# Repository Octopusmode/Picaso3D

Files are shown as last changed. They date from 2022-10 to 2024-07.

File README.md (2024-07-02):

# Typing SVG (https://git.io/typing-svg)

В этом репозитории находятся полезные ресурсы для принтеров [Picaso3D](https://picaso-3d.ru/ru/techsupport/).

Репозиторий поддерживается участниками телеграм-группы [Picaso3dUnofficial](https://t.me/Picaso3dUnofficial).

Официальный сайт [Центра поддержки Picaso3D](http://helpcenter.picaso-3d.ru/).

## Содержимое репозитория:
#### :large_blue_circle: [Hardware (Фотографии плат, покупные радиоэлементы)](./Hardware)
---
  * [DES](./Hardware/DES_Hardware)
  * [DPXL](./Hardware/DPXL_Hardware)
  * [DXL](./Hardware/DXL_Hardware)
  * [DPX](./Hardware/DPX_Hardware)
    * [DPX_DPXL_Мотор_переключения_сопел](./Hardware/DPX_Hardware/DPX_DPXL_Мотор_переключения_сопел)
    * [DPX_Electronic_components](./Hardware/DPX_Hardware/DPX_Electronic_components)
    * [DPX_Motherboard](./Hardware/DPX_Hardware/DPX_Motherboard)
    * [DPX_Ремень](./Hardware/DPX_Hardware/DPX_Ремень)
    * [DPX_Энкодер](./Hardware/DPX_Hardware/DPX_Энкодер)
  * [DPX_S2](./Hardware/DPX_S2_Hardware)
  * [DXL_S2](./Hardware/DXL_S2_Hardware)
  * [DX](./Hardware/DX_Hardware)
  * [DX_S2](./Hardware/DX_S2_Hardware)
  * [PRO250](./Hardware/PRO250_Hardware)
 * [Покупные_радиоэлементы_разное](./Hardware/Покупные_радиоэлементы_разное)
    * [Муфта](./Hardware/Покупные_радиоэлементы_разное/Муфта)
    * [Ссылки](./Hardware/Покупные_радиоэлементы_разное/Ссылки)
    * [Фотографии](./Hardware/Покупные_радиоэлементы_разное/Фотографии)

#### :large_blue_circle: [Software (Программное обеспечение, прошивки)](./Software)
---
  * [PRO250_EEPROM](./Software/PRO250_EEPROM_(uc))
  * [PRO250_Прошивки](./Software/PRO250_Прошивки)
  * [DES_Klipper_cfg](./Software/DES_Klipper_cfg)
  * [DES_Marlin_cfg](./Software/DES_Marlin_cfg)
  * [DES_Прошивка](./Software/DES_Прошивка)
  * [XPRO_Прошивки](./Software/XPRO_Прошивки)
  * [PolygonX](./Software/PolygonX)
  * [PRO250_Klipper_(external_link)](https://github.com/Octopusmode/pro250)
  * [Утилита_для_удаленной_печати_(external_link)](https://github.com/olegh/pxctl) 

#### :large_blue_circle: STL-файлы для ремонта принтера, тюнинга, файлы для калибровки
---
  * [STL_Детали_принтеров](./STL_Детали_принтеров)
<details>
<summary> Список файлов в папке "STL_Детали_принтеров" </summary>
 
   * [PRO250](./STL_Детали_принтеров/PRO250)
     * [PRO250_HolderUpgrade](./STL_Детали_принтеров/PRO250/PRO250_HolderUpgrade)
     * [PRO250_Filament_Feeder](./STL_Детали_принтеров/PRO250/PRO250_Filament_Feeder.stl)
     * [PRO250_Y_endstop](./STL_Детали_принтеров/PRO250/PRO250_Y_endstop.stl)
     * [PRO250_Y_Shaft_holder](./STL_Детали_принтеров/PRO250/PRO250_Y_Shaft_holder.stl)
     * [PRO250_Кронштейн](./STL_Детали_принтеров/PRO250/PRO250_Кронштейн.stl)
     * [PRO250_Крутилка_стола](./STL_Детали_принтеров/PRO250/PRO250_Крутилка_стола.stl)
     * [PRO250_Сборка_головы](./STL_Детали_принтеров/PRO250/PRO250_Сборка_головы.stp)
     * [PRO250_Центральная_шестерня.pdf](./STL_Детали_принтеров/PRO250/PRO250_Центральная_шестерня.pdf)
     * [DPS_004.10.08_Филамент](./STL_Детали_принтеров/PRO250/DPS_004.10.08_Филамент.stl)
     * [Держатель_очистителя_PRO250_под_очиститель_X_PRO_repaired_fixed](./STL_Детали_принтеров/PRO250/Держатель_очистителя_PRO250_под_очиститель_X_PRO_repaired_fixed.stl)
     * [Контейнер_под_держатель_чистика](./STL_Детали_принтеров/PRO250/Контейнер_под_держатель_чистика.stl)
     * [Упор_концевика](./STL_Детали_принтеров/PRO250/Упор_концевика.stl)
     * [Шайба_двигателя_переключения_сопел](./STL_Детали_принтеров/PRO250/Шайба_двигателя_переключения_сопел.stl)
  * [Designer](./STL_Детали_принтеров/Designer)
  * [DES_Кронштейн](./STL_Детали_принтеров/DES_Кронштейн.stl)
  * [DES_Проставка_экструдер](./STL_Детали_принтеров/DES_Проставка_экструдер.stl)
  * [DESС_00.00.03_Петля_верхняя_скрытая](./STL_Детали_принтеров/DESС_00.00.03_Петля_верхняя_скрытая.stl)
  * [DESС_00.00.04_Петля_нижняя_скрытая](./STL_Детали_принтеров/DESС_00.00.04_Петля_нижняя_скрытая.stl)
  * [DESС_00.00.06_Петля_средняя_скрытая](./STL_Детали_принтеров/DESС_00.00.06_Петля_средняя_скрытая.stl)
  * [DPS_004.10.08_Филамент](./STL_Детали_принтеров/DPS_004.10.08_Филамент.stl)
  * [DPS_004.10.09_Держатель_трубок](./STL_Детали_принтеров/DPS_004.10.09_Держатель_трубок.stl)
  * [DPS_01.00.14_Левый_зажим_эксцентрик](./STL_Детали_принтеров/DPS_01.00.14_Левый_зажим_эксцентрик.stl)
  * [DPS_01.00.14_Правый_зажим_эксцентрик.](./STL_Детали_принтеров/DPS_01.00.14_Правый_зажим_эксцентрик.stl)
  * [DPS_02.00.02_01_Стойка_для_валов_XY](./STL_Детали_принтеров/DPS_02.00.02_01_Стойка_для_валов_XY.stl)
  * [DPS_02.00.08.01_Держатель_трубки](./STL_Детали_принтеров/DPS_02.00.08.01_Держатель_трубки.stl)
  * [DPS_02.00.08_01_Держатель_трубки_](./STL_Детали_принтеров/DPS_02.00.08_01_Держатель_трубки_.stl)
  * [DPS_02.00.09_Держатель_чистика](./STL_Детали_принтеров/DPS_02.00.09_Держатель_чистика.stl)
  * [DEX_Фиксатор_трубки_подачи_пластика](./STL_Детали_принтеров/DEX_Фиксатор_трубки_подачи_пластика.stl)  
  * [DPX_00.00.05_Держатель_катушки](./STL_Детали_принтеров/DPX_00.00.05_Держатель_катушки.stl)
  * [DPX_02.00.02_Держатель_роликов_левый](./STL_Детали_принтеров/DPX_02.00.02_Держатель_роликов_левый.stl)
  * [DPX_02.00.03_Держатель_роликов_правый](./STL_Детали_принтеров/DPX_02.00.03_Держатель_роликов_правый.stl)
  * [DPX_02.00.04_Втулка_правого_держателя](./STL_Детали_принтеров/DPX_02.00.04_Втулка_правого_держателя.stl)
  * [DPX_02.00.05_Втулка_дистанционная_new](./STL_Детали_принтеров/DPX_02.00.05_Втулка_дистанционная_new.stl)
  * [DPX_02.00.16_Держатель_чистика_V1](./STL_Детали_принтеров/DPX_02.00.16_Держатель_чистика_V1.stl)
  * [DPX_04.00.03_Крутилка](./STL_Детали_принтеров/DPX_04.00.03_Крутилка.stl)
  * [DPX_Держатель_пружины](./STL_Детали_принтеров/DPX_Держатель_пружины.stl)
  * [DPX_Держатель_трубки_v1](./STL_Детали_принтеров/DPX_Держатель_трубки_v1.stl)
  * [DPX_Фиксатор_трубок_подачи_пластика](./STL_Детали_принтеров/DPX_Фиксатор_трубок_подачи_пластика.stl)
  * [DPX_Чистик](./STL_Детали_принтеров/DPX_Чистик.stl)
  * [DPX_Блоки_энкодеров_S1_S2](./STL_Детали_принтеров/DPX_Блоки_энкодеров_S1_S2)
  * [DXL_DPXL_Боковой_фиксатор_трубки_подачи_пластика](./STL_Детали_принтеров/DXL_DPXL_Боковой_фиксатор_трубки_подачи_пластика.stl)
  * [DXL_Воздуховод](./STL_Детали_принтеров/DXL_Воздуховод.stl)
  * [DXL_Воздуховод_short](./STL_Детали_принтеров/DXL_Воздуховод_short.stl)
  * [DXL_Заглушка](./STL_Детали_принтеров/DXL_Заглушка.stl)
  * [DXL_Фиксатор_винта_М4](./STL_Детали_принтеров/DXL_Фиксатор_винта_М4.stl)
  * [DXL_Блок_энкодера](./STL_Детали_принтеров/DXL_Блок_энкодера)
  * [DPXL_Фиксатор_прижимного_винта_М4.](./STL_Детали_принтеров/DPXL_Фиксатор_прижимного_винта_М4.stl)
  * [DX_02.00.09_Держатель_чистика.](./STL_Детали_принтеров/DX_02.00.09_Держатель_чистика.stl)
  * [DX_radfan_v1.0](./STL_Детали_принтеров/DX_radfan_v1.0.stl)
  * [DX_Держатель_прижимной_пружины](./STL_Детали_принтеров/DX_Держатель_прижимной_пружины.stl)
  * [DX_Держатель_пружины](./STL_Детали_принтеров/DX_Держатель_пружины.stl)
  * [DX_Блок_энкодера_Корпус](./STL_Детали_принтеров/DX_Блок_энкодера_Корпус)
  * [DX_Проставка_радиатора](./STL_Детали_принтеров/DX_Проставка_радиатора)
  * [DX_DPX_Рычаг_диска_энкодера](./STL_Детали_принтеров/DX_DPX_Рычаг_диска_энкодера.stl)
  * [SDX_Направляющая_пластика](./STL_Детали_принтеров/SDX_Направляющая_пластика.stl)
  * [SDPX_Корпус_блока_энкодеров](./STL_Детали_принтеров/SDPX_Корпус_блока_энкодеров.stl)
  * [Воздуховод](./STL_Детали_принтеров/Воздуховод.stl)
  * [Деталь_филамента](./STL_Детали_принтеров/Деталь_филамента.stl)
  * [Кронштейн_для_кабель_канала](./STL_Детали_принтеров/Кронштейн_для_кабель_канала.stl)
  * [Петля_в_сборе](./STL_Детали_принтеров/Петля_в_сборе.stl)
  * [Сухари](./STL_Детали_принтеров/Сухари)
  * [Шайба_двигателя_переключения_сопел](./STL_Детали_принтеров/Шайба_двигателя_переключения_сопел.stl)
  * [Шайба_двигателя_переключения_сопел](./STL_Детали_принтеров/Шайба_двигателя_переключения_сопел) 
</details>

  * [STL_Калибровочные_шаблоны](./STL_Калибровочные_шаблоны)

<details>
<summary> Список файлов в папке "STL_Калибровочные_шаблоны" </summary>
 
  * [PRO250_Сведение_сопел](./STL_Калибровочные_шаблоны/PRO250_Сведение_сопел)
  * [PRO250_Тест_ремней](./STL_Калибровочные_шаблоны/PRO250_Тест_ремней)
  * [Калибровочный_шаблон_очистителя](./STL_Калибровочные_шаблоны/Калибровочный_шаблон_очистителя.stl)
  * [Калибровочный_шаблон_очистителя_0XYn](./STL_Калибровочные_шаблоны/Калибровочный_шаблон_очистителя_0XYn.stl)
  * [Калибровочный_шаблон_очистителя_XY0.plgx](./STL_Калибровочные_шаблоны/Калибровочный_шаблон_очистителя_XY0.plgx)
  * [Настройка_прижима](./STL_Калибровочные_шаблоны/Настройка_прижима.stl)
  * [Настройка_прижима_200x200](./STL_Калибровочные_шаблоны/Настройка_прижима_200x200.stl)
  * [Настройка_прижима_куб_2х2х2](./STL_Калибровочные_шаблоны/Настройка_прижима_куб_2х2х2.stl)
  * [Настройка_прижима_ХPRO_0.25.plgx](./STL_Калибровочные_шаблоны/Настройка_прижима_ХPRO_0.25.plgx)
  * [Сведение_сопел_0.3.plgx](./STL_Калибровочные_шаблоны/Сведение_сопел_0.3.plgx)
  * [Сведение_сопел_ABS.plg](./STL_Калибровочные_шаблоны/Сведение_сопел_ABS.plg)
  * [Сведение_сопел_PLA.plg](./STL_Калибровочные_шаблоны/Сведение_сопел_PLA.plg)
  * [Сведение_сопел_грубо.plgx](./STL_Калибровочные_шаблоны/Сведение_сопел_грубо.plgx)
  * [Сведение_сопел_грубо_полный.plgx](./STL_Калибровочные_шаблоны/Сведение_сопел_грубо_полный.plgx)
  * [Сведение_сопел_кольца_0_25_0_5.plgx](./STL_Калибровочные_шаблоны/Сведение_сопел_кольца_0_25_0_5.plgx)
</details>

  * [STL_Тюнинг](./STL_Тюнинг)
<details>
<summary> Список файлов в папке "STL_Тюнинг" </summary>
 
  * [DPXL_Фиксатор_трубок_подачи_пластика](./STL_Тюнинг/DPXL_Фиксатор_трубок_подачи_пластика)
  * [DPX_Фиксатор_трубок_подачи_пластика_mod3](./STL_Тюнинг/DPX_Фиксатор_трубок_подачи_пластика_mod3)
  * [DPX_S2_Фиксатор_трубок_подачи_пластика](./STL_Тюнинг/DPX_S2_Фиксатор_трубок_подачи_пластика)
  * [DX_S2_Фиксатор_трубок_подачи_пластика](./STL_Тюнинг/DX_S2_Фиксатор_трубок_подачи_пластика)
  * [DX_Вентиляторы_обдува_детали](./STL_Тюнинг/DX_Вентиляторы_обдува_детали)
  * [DX_Фиксатор_трубок_подачи_для_Формакс](./STL_Тюнинг/DX_Фиксатор_трубок_подачи_для_Формакс)
  * [DXL_DPXL_Крепление_стекла](./STL_Тюнинг/DXL_DPXL_Крепление_стекла)
  * [DXL_DPXL_Центровщик_флешки_для_принтера](./STL_Тюнинг/DXL_DPXL_Центровщик_флешки_для_принтера.stl)
  * [DXL_Воздухоотвод_для_принтера](./STL_Тюнинг/DXL_Воздухоотвод_для_принтера.stl)
  * [Контейнеры_для_мусора](./STL_Тюнинг/Контейнеры_для_мусора)
  * [Крепление_трубки_подачи](./STL_Тюнинг/Крепление_трубки_подачи)
  * [Кронштейн_для_катушки_0](./STL_Тюнинг/Кронштейн_для_катушки_0)
  * [Кронштейн_для_катушки_1](./STL_Тюнинг/Кронштейн_для_катушки_1)
  * [Кронштейн_для_катушки_3](./STL_Тюнинг/Кронштейн_для_катушки_3)
  * [Кронштейн_для_катушки_4](./STL_Тюнинг/Кронштейн_для_катушки_4)
  * [Кронштейн_для_катушки_5](./STL_Тюнинг/Кронштейн_для_катушки_5)
  * [Фильтры_пыли](./STL_Тюнинг/Фильтры_пыли)
  * [Filament_tube_feeder](./STL_Тюнинг/Filament_tube_feeder.stl)
  * [Держатель_для_ключа_сопла](./STL_Тюнинг/Держатель_для_ключа_сопла.stl)
</details>

#### :large_blue_circle: Инструкции
---
  * [Подшипники_S1](./Подшипники_S1)
  * [Инструкции](./Инструкции)

<details>
<summary> Список инструкций </summary>
 
  * [Builder_Picaso_инструкция.pdf](./Инструкции/Builder_Picaso_инструкция.pdf)
  * [DES_PRO250_Замена_ремней](./Инструкции/DES_PRO250_Замена_ремней)
  * [DES_PRO250_Ошибка_DEF_DEF.pdf](./Инструкции/DES_PRO250_Ошибка_DEF_DEF.pdf)
  * [DES_PRO250_Почему_не_подается_пластик.pdf](./Инструкции/DES_PRO250_Почему_не_подается_пластик.pdf)
  * [DES_PRO250_Сборка_нагревателя.pdf](./Инструкции/DES_PRO250_Сборка_нагревателя.pdf)
  * [DES_Замена_роликов_швеллер.pdf](./Инструкции/DES_Замена_роликов_швеллер.pdf)
  * [DES_Прочистка_трубки_нагревательного_элемента.pdf](./Инструкции/DES_Прочистка_трубки_нагревательного_элемента.pdf)
  * [PRO250_Калибровка_сопел_совмещение.pdf](./Инструкции/PRO250_Калибровка_сопел_совмещение.pdf)
  * [PRO250_Настройка_датчика_стола.pdf](./Инструкции/PRO250_Настройка_датчика_стола.pdf)
  * [PRO250_Проверка_напряжений_на_моторах.pdf](./Инструкции/PRO250_Проверка_напряжений_на_моторах.pdf)
  * [PRO250_Прочистка_нагревателя.pdf](./Инструкции/PRO250_Прочистка_нагревателя.pdf)
  * [PRO250_Разборка_головы.pdf](./Инструкции/PRO250_Разборка_головы.pdf)
  * [PRO250_Утилита_Service_exe_Калибровка_сопел_совмещение](./Инструкции/PRO250_Утилита_Service_exe_Калибровка_сопел_совмещение)
  * [X_Диагностика_блока_энкодеров.pdf](./Инструкции/X_Диагностика_блока_энкодеров.pdf)
  * [X_XPRO_Замена_заднего_крепления_стекла_.pdf](./Инструкции/X_XPRO_Замена_заднего_крепления_стекла_.pdf)
  * [X_XPRO_Настройка_стола.docx.pdf](./Инструкции/X_XPRO_Настройка_стола.docx.pdf)
  * [XPRO_Неполный_разбор_печатающей_головы.pdf](./Инструкции/XPRO_Неполный_разбор_печатающей_головы.pdf)
  * [XPRO_Проверка_замена_роликов_и_ремней.pdf](./Инструкции/XPRO_Проверка_замена_роликов_и_ремней.pdf)
  * [XPRO_Прочистка_нагревателя.pdf](./Инструкции/XPRO_Прочистка_нагревателя.pdf)
  * [XPRO_Список_ошибок.pdf](./Инструкции/XPRO_Список_ошибок.pdf)
  * [XL_XLPRO_Настройка_ШВП.pdf](./Инструкции/XL_XLPRO_Настройка_ШВП.pdf)
  * [Инструкция_по_упаковке_принтеров.pdf](./Инструкции/Инструкция_по_упаковке_принтеров.pdf)
  * [Инструкция_ШС_Шкаф_Сушильный.pdf](./Инструкции/Инструкция_ШС_Шкаф_Сушильный.pdf)

 </details>

#### :large_blue_circle: Настройки слайсеров, профили пластиков
---
  * [Cura](./_Cura)
  * [S3D_для_Picaso_Статья_о_настройке](./_S3D_для_Picaso_Статья_о_настройке)
  * [Профили_Polygon_XPRO](./Профили_пластиков_S3D_Polygon/Профили_Polygon_XPRO)

<details>
<summary>Список профилей для Polygon для XPRO</summary>

1. ABSM_PETG
1. BESTF_ABS
1. BESTF_PLA_BLACK
1. ESUN_ABS
1. ESUN_PLA_200
1. ESUN_PLA
1. FILM_CERAMO
1. FILM_SBS
1. FLEX_HARD PprintProduct
1. NYLON_MOD_PprintProduct
1. NYLON STRONG_PP
1. PICASO_ABS
1. PICASO_HIPS
1. PICASO_PLA
1. PICASO PVA(ESUN)
1. PICASO_PVA(REC)
1. PLA_PrintProduct
1. REC_ABS
1. REC_FLEX
1. REC_HIPS
1. REC_PLA
1. TAULMAN_910
1. U3PRINT_PC
1. VOLPRINT_PLA

</details>

  * [Профили_Simplify3D](./Профили_пластиков_S3D_Polygon/Профили_Simplify3D)

<details>
<summary>Список профилей для Simplify3D для DPX, DX</summary>

1. all_profiles_DX_DXP.factory
1. Picaso_DPX_ABS-PA+HIPS_script.fff
1. Picaso_DPX_FlexHARD+PLA(F).fff
1. Picaso_DPX_F_WAX3D.fff
1. Picaso_DPX_GF4+HIPS_script.fff
1. Picaso_DPX_PETG(BF)+PLA(F).fff
1. Picaso_DPX_PETG+PLA(F)_script.fff
1. Picaso_DPX_PLA+PVA(eSUN).fff
1. Picaso_DPX_PLA+PVA(REC).fff
1. Picaso_DPX_TPU(A75)+PLA(F).fff
1. Picaso_DPX_TPU(A80)+PLA(F).fff
1. Picaso_DPX_TPU(A93)+PLA(F).fff
1. Picaso_DX_ABS_LITHOPANE.fff
1. Picaso_DX_BF_PLA.fff
1. Picaso_DX_CLOTHO-ABS-GF13.fff
1. Picaso_DX_eSUN_ePA-CF.fff
1. Picaso_DX_FD_TPU-A75.fff
1. Picaso_DX_F_ABS-PA-GF8.fff
1. Picaso_DX_F_ABS-PA.fff
1. Picaso_DX_F_ABS.fff
1. Picaso_DX_F_CERAMO.fff
1. Picaso_DX_F_GF4.fff
1. Picaso_DX_F_PA66-GF30.fff
1. Picaso_DX_F_PBT-GF30.fff
1. Picaso_DX_F_PETg.fff
1. Picaso_DX_F_PLA.fff
1. Picaso_DX_F_PP-GF30.fff
1. Picaso_DX_F_PP.fff
1. Picaso_DX_F_PRO-FLEX.fff
1. Picaso_DX_F_SBS.fff
1. Picaso_DX_F_TERMAX-GF40.fff
1. Picaso_DX_F_TITAN_ABS-GF12.fff
1. Picaso_DX_F_TPU-A80.fff
1. Picaso_DX_F_TPU-A93.fff
1. Picaso_DX_F_TPU-CF5.fff
1. Picaso_DX_F_TPU-GF10.fff
1. Picaso_DX_F_TPU-GF30.fff
1. Picaso_DX_HTP_NYLON.fff
1. Picaso_DX_IGUS_J260.fff
1. Picaso_DX_PrPr_FlexHARD.fff
1. Picaso_DX_REC_FORMAX.fff
1. Picaso_DX_REC_RUBBER.fff
1. Picaso_DX_REC_TPU-D70.fff

</details>

  * [Профили_Simplify_PRO250](./Профили_пластиков_S3D_Polygon/Профили_Simplify_PRO250)

<details>
<summary>Список профилей для Simplify3D для PRO250</summary>

1. Picaso ABS 0.8.fff
1. PICASO ABS 2 heads support dens.fff
1. Picaso Designer PRO250.fff
1. PICASO DUAL COLOR.fff
1. PRO250 ABS 0.3 color_A.fff
1. PRO250 ABS 0.3 color_B.fff
1. PRO250 ABS 1 head 0.3.fff
1. PRO250 ABS_HIPS 2hds 85dens.fff
1. PRO250 ABS_PC 0.3 1extruder.fff
1. PRO250 SBS 0.8 transparent-Bottle Small.fff
1. PRO250 SBS 0.8 transparent-Bottle.fff

</details>

#### :large_blue_circle: Ремонт, тюнинг
---
  * [Сопливчик_форма_для_литья](./Сопливчик_форма_для_литья)
  * [Стёкла](./Стёкла)
    * [250PRO_стекло_0.jpg](./Стёкла/img/250PRO_стекло_0.jpg)
    * [250PRO_стекло_1.jpg](./Стёкла/img/250PRO_стекло_1.jpg)
    * [XPRO_Стекло_0.jpg](./Стёкла/img/XPRO_Стекло_0.jpg)
    * [XPRO_Стекло_1.jpg](./Стёкла/img/XPRO_Стекло_1.jpg)
    * [XL_glass.jpg](./Стёкла/img/XL_glass.jpg)
  * [Листы_PEI](./Листы_PEI)
  * [Тензодатчик](./Тензодатчик)

#### :large_blue_circle: Справочное
---
  * [Сушка_пластика](./Сушка_пластика)
  * [Термопаста_смазки](./Термопаста_смазки) 
  * [Размеры_масса_катушек_филамента.xlsx](./Размеры_масса_катушек_филамента.xlsx)

#### :large_blue_circle: Разное
---
  * [Картонная_катушка_HTP](./Картонная_катушка_HTP)
  * [Несортированное](./Несортированное)

#### :large_blue_circle: Используемые сокращения
---
> **PRO250** Designer PRO250
> 
> **DES** Designer
> 
> **DESC** Designer Classic
> 
> **DX** Designer X
> 
> **DXPRO DPX** Designer X PRO
>
> **DXL** Designer XL
>
> **DXLPRO DPXL** Designer XL PRO
>
> **SDPX** Designer X PRO S2
>
> **SDX** Designer X S2

> Информация о принтерах X, XPRO, XL, XLPRO без пометки «S2» относится к принтерам серии «S1».

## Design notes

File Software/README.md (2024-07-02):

# Software/программное обеспечение принтеров Picaso

В данном разделе хранятся:

+ конфиги прошивок Marlin, Klipper для родных плат принтера Picaso Designer;

+ файлы прошивок принтеров, в том числе PRO250;

+ файлы старых версий PolygonX;

+ прочее, связанное с программным обеспечением принтеров.

Внешние ссылки:

 * PRO250_Klipper: https://github.com/Octopusmode/pro250

 * Утилита_для_удаленной_печати: https://github.com/olegh/pxctl

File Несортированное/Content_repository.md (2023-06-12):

# Содержимое репозитория:

## [Firmware (Фотографии плат, покупные радиоэлементы)](./Firmware)

  * [DES](./Firmware/DES_Firmware)
  * [DPXL](.Firmware/DPXL_Firmware)
    * [XLPRO_XPRO_Мотор_переключения_сопел](./Firmware/DPXL_Firmware/XLPRO_XPRO_Мотор_переключения_сопел.lnk)
  * [DPX](./Firmware/DPX_Firmware_(under_construction))
    * [DPX_DPXL_Мотор_переключения_сопел](./Firmware/DPX_Firmware_(under_construction)/DPX_DPXL_Мотор_переключения_сопел)
    * [DPX_Electronic_components](./Firmware/DPX_Firmware_(under_construction)/DPX_Electronic_components)
    * [DPX_Motherboard](./Firmware/DPX_Firmware_(under_construction)/DPX_Motherboard)
    * [DPX_Ремень](./Firmware/DPX_Firmware_(under_construction)/DPX_Ремень)
    * [DPX_Энкодер](./Firmware/DPX_Firmware_(under_construction)/DPX_Энкодер)
  * [DPX_S2](./Firmware/DPX_S2_Firmware)
  * [DXL_S2](./Firmware/DXL_S2_Firmware)
  * [DX](./Firmware/DX_Firmware_(under_construction))
  * [DX_S2](./Firmware/DX_S2_Firmware)
  * [PRO250](./Firmware/PRO250_Firmware)
  * [Покупные_радиоэлементы_разное](./Firmware/Покупные_радиоэлементы_разное)
    * [Муфта](./Firmware/Покупные_радиоэлементы_разное/Муфта)
    * [Ссылки](./Firmware/Покупные_радиоэлементы_разное/Ссылки)
    * [Фотографии](./Firmware/Покупные_радиоэлементы_разное/Фотографии)

## [Software (Программное обеспечение, прошивки)](./Software)

  * [PRO250_EEPROM](./Software/PRO250_EEPROM (uc))
  * [PRO250_Прошивки](./Software/PRO250_Прошивки)
  * [DES_Klipper_cfg](./Software/DES_Klipper_cfg)
  * [DES_Marlin_cfg](./Software/DES_Marlin_cfg)
  * [XPRO_Прошивки](./Software/XPRO_Прошивки)
  * [PolygonX](./Software/PolygonX)

## STL-файлы для ремонта принтера, тюнинга, файлы для калибровки

### [STL_Детали_принтеров](./STL_Детали_принтеров)

   * [PRO250](./STL_Детали_принтеров/PRO250)
     * [PRO250_HolderUpgrade](./STL_Детали_принтеров/PRO250/PRO250_HolderUpgrade)
     * [PRO250_Filament_Feeder](./STL_Детали_принтеров/PRO250/PRO250_Filament_Feeder.stl)
     * [PRO250_Y_endstop](./STL_Детали_принтеров/PRO250/PRO250_Y_endstop.stl)
     * [PRO250_Y_Shaft_holder](./STL_Детали_принтеров/PRO250/PRO250_Y_Shaft_holder.stl)
     * [PRO250_Кронштейн](./STL_Детали_принтеров/PRO250/PRO250_Кронштейн.stl)
     * [PRO250_Крутилка_стола](./STL_Детали_принтеров/PRO250/PRO250_Крутилка_стола.stl)
     * [PRO250_Сборка_головы](./STL_Детали_принтеров/PRO250/PRO250_Сборка_головы.stp)
     * [PRO250_Центральная_шестерня.pdf](./STL_Детали_принтеров/PRO250/PRO250_Центральная_шестерня.pdf)
     * [DPS_004.10.08_Филамент](./STL_Детали_принтеров/PRO250/DPS_004.10.08_Филамент.stl)
     * [Держатель_очистителя_PRO250_под_очиститель_X_PRO_repaired_fixed](./STL_Детали_принтеров/PRO250/Держатель_очистителя_PRO250_под_очиститель_X_PRO_repaired_fixed.stl)
     * [Контейнер_под_держатель_чистика](./STL_Детали_принтеров/PRO250/Контейнер_под_держатель_чистика.stl)
     * [Упор_концевика](./STL_Детали_принтеров/PRO250/Упор_концевика.stl)
     * [Шайба_двигателя_переключения_сопел](./STL_Детали_принтеров/PRO250/Шайба_двигателя_переключения_сопел.stl)
  
  * [DES_Кронштейн](./STL_Детали_принтеров/DES_Кронштейн.stl)
  * [DES_Проставка_экструдер](./STL_Детали_принтеров/DES_Проставка_экструдер.stl)

  * [DESС_00.00.03_Петля_верхняя_скрытая](./STL_Детали_принтеров/DESС_00.00.03_Петля_верхняя_скрытая.stl)
  * [DESС_00.00.04_Петля_нижняя_скрытая](./STL_Детали_принтеров/DESС_00.00.04_Петля_нижняя_скрытая.stl)
  * [DESС_00.00.06_Петля_средняя_скрытая](./STL_Детали_принтеров/DESС_00.00.06_Петля_средняя_скрытая.stl)

  * [DPS_004.10.08_Филамент](./STL_Детали_принтеров/DPS_004.10.08_Филамент.stl)
  * [DPS_004.10.09_Держатель_трубок](./STL_Детали_принтеров/DPS_004.10.09_Держатель_трубок.stl)
  * [DPS_01.00.14_Левый_зажим_эксцентрик](./STL_Детали_принтеров/DPS_01.00.14_Левый_зажим_эксцентрик.stl)
  * [DPS_01.00.14_Правый_зажим_эксцентрик.](./STL_Детали_принтеров/DPS_01.00.14_Правый_зажим_эксцентрик.stl)
  * [DPS_02.00.02_01_Стойка_для_валов_XY](./STL_Детали_принтеров/DPS_02.00.02_01_Стойка_для_валов_XY.stl)
  * [DPS_02.00.08.01_Держатель_трубки](./STL_Детали_принтеров/DPS_02.00.08.01_Держатель_трубки.stl)
  * [DPS_02.00.08_01_Держатель_трубки_](./STL_Детали_принтеров/DPS_02.00.08_01_Держатель_трубки_.stl)
  * [DPS_02.00.09_Держатель_чистика](./STL_Детали_принтеров/DPS_02.00.09_Держатель_чистика.stl)

  * [DEX_Фиксатор_трубки_подачи_пластика](./STL_Детали_принтеров/DEX_Фиксатор_трубки_подачи_пластика.stl)  
  * [DPX_00.00.05_Держатель_катушки](./STL_Детали_принтеров/DPX_00.00.05_Держатель_катушки.stl)
  * [DPX_02.00.02_Держатель_роликов_левый](./STL_Детали_принтеров/DPX_02.00.02_Держатель_роликов_левый.stl)
  * [DPX_02.00.03_Держатель_роликов_правый](./STL_Детали_принтеров/DPX_02.00.03_Держатель_роликов_правый.stl)
  * [DPX_02.00.04_Втулка_правого_держателя](./STL_Детали_принтеров/DPX_02.00.04_Втулка_правого_держателя.stl)
  * [DPX_02.00.05_Втулка_дистанционная_new](./STL_Детали_принтеров/DPX_02.00.05_Втулка_дистанционная_new.stl)
  * [DPX_02.00.16_Держатель_чистика_V1](./STL_Детали_принтеров/DPX_02.00.16_Держатель_чистика_V1.stl)
  * [DPX_04.00.03_Крутилка](./STL_Детали_принтеров/DPX_04.00.03_Крутилка.stl)
  * [DPX_Держатель_пружины](./STL_Детали_принтеров/DPX_Держатель_пружины.stl)
  * [DPX_Держатель_трубки_v1](./STL_Детали_принтеров/DPX_Держатель_трубки_v1.stl)
  * [DPX_Фиксатор_трубок_подачи_пластика](./STL_Детали_принтеров/DPX_Фиксатор_трубок_подачи_пластика.stl)
  * [DPX_Чистик](./STL_Детали_принтеров/DPX_Чистик.stl)
  * [DPX_Блоки_энкодеров_S1_S2](./STL_Детали_принтеров/DPX_Блоки_энкодеров_S1_S2)
  * [DPX_Направляющая_трубки_подачи_пластика](./STL_Детали_принтеров/DPX_Направляющая_трубки_подачи_пластика)

  * [DXL_DPXL_Боковой_фиксатор_трубки_подачи_пластика](./STL_Детали_принтеров/DXL_DPXL_Боковой_фиксатор_трубки_подачи_пластика.stl)
  * [DXL_Воздуховод](./STL_Детали_принтеров/DXL_Воздуховод.stl)
  * [DXL_Воздуховод_short](./STL_Детали_принтеров/DXL_Воздуховод_short.stl)
  * [DXL_Заглушка](./STL_Детали_принтеров/DXL_Заглушка.stl)
  * [DXL_Фиксатор_винта_М4](./STL_Детали_принтеров/DXL_Фиксатор_винта_М4.stl)
  * [DXL_Блок_энкодера](./STL_Детали_принтеров/DXL_Блок_энкодера)
  * [DPXL_Фиксатор_прижимного_винта_М4.](./STL_Детали_принтеров/DPXL_Фиксатор_прижимного_винта_М4.stl)

  * [DX_02.00.09_Держатель_чистика.](./STL_Детали_принтеров/DX_02.00.09_Держатель_чистика.stl)
  * [DX_radfan_v1.0](./STL_Детали_принтеров/DX_radfan_v1.0.stl)
  * [DX_Держатель_прижимной_пружины](./STL_Детали_принтеров/DX_Держатель_прижимной_пружины.stl)
  * [DX_Держатель_пружины](./STL_Детали_принтеров/DX_Держатель_пружины.stl)
  * [DX_Блок_энкодера_Корпус](./STL_Детали_принтеров/DX_Блок_энкодера_Корпус)
  * [DX_Проставка_радиатора](./STL_Детали_принтеров/DX_Проставка_радиатора)

  * [Воздуховод](./STL_Детали_принтеров/Воздуховод.stl)
  * [Деталь_филамента](./STL_Детали_принтеров/Деталь_филамента.stl)
  * [Кронштейн_для_кабель_канала](./STL_Детали_принтеров/Кронштейн_для_кабель_канала.stl)
  * [Петля_в_сборе](./STL_Детали_принтеров/Петля_в_сборе.stl)
  * [Сухари](./STL_Детали_принтеров/Сухари)
  * [Шайба_двигателя_переключения_сопел](./STL_Детали_принтеров/Шайба_двигателя_переключения_сопел.stl)
  * [Шайба_двигателя_переключения_сопел](./STL_Детали_принтеров/Шайба_двигателя_переключения_сопел) 

### [STL_Калибровочные_шаблоны](./STL_Калибровочные_шаблоны)
 
  * [PRO250_Сведение_сопел](./STL_Калибровочные_шаблоны/PRO250_Сведение_сопел)
  * [PRO250_Тест_ремней](./STL_Калибровочные_шаблоны/PRO250_Тест_ремней)
  * [Калибровочный_шаблон_очистителя](./STL_Калибровочные_шаблоны/Калибровочный_шаблон_очистителя.stl)
  * [Калибровочный_шаблон_очистителя_0XYn](./STL_Калибровочные_шаблоны/Калибровочный_шаблон_очистителя_0XYn.stl)
  * [Калибровочный_шаблон_очистителя_XY0.plgx](./STL_Калибровочные_шаблоны/Калибровочный_шаблон_очистителя_XY0.plgx)
  * [Настройка_прижима](./STL_Калибровочные_шаблоны/Настройка_прижима.stl)
  * [Настройка_прижима_200x200](./STL_Калибровочные_шаблоны/Настройка_прижима_200x200.stl)
  * [Настройка_прижима_куб_2х2х2](./STL_Калибровочные_шаблоны/Настройка_прижима_куб_2х2х2.stl)
  * [Настройка_прижима_ХPRO_0.25.plgx](./STL_Калибровочные_шаблоны/Настройка_прижима_ХPRO_0.25.plgx)
  * [Сведение_сопел_0.3.plgx](./STL_Калибровочные_шаблоны/Сведение_сопел_0.3.plgx)
  * [Сведение_сопел_ABS.plg](./STL_Калибровочные_шаблоны/Сведение_сопел_ABS.plg)
  * [Сведение_сопел_PLA.plg](./STL_Калибровочные_шаблоны/Сведение_сопел_PLA.plg)
  * [Сведение_сопел_грубо.plgx](./STL_Калибровочные_шаблоны/Сведение_сопел_грубо.plgx)
  * [Сведение_сопел_грубо_полный.plgx](./STL_Калибровочные_шаблоны/Сведение_сопел_грубо_полный.plgx)
  * [Сведение_сопел_кольца_0_25_0_5.plgx](./STL_Калибровочные_шаблоны/Сведение_сопел_кольца_0_25_0_5.plgx)

### [STL_Тюнинг](./STL_Тюнинг)
 
  * [DPXL_Фиксатор_трубок_подачи_пластика](./STL_Тюнинг/DPXL_Фиксатор_трубок_подачи_пластика)
  * [DPX_Фиксатор_трубок_подачи_пластика_mod3](./STL_Тюнинг/DPX_Фиксатор_трубок_подачи_пластика_mod3)

  * [DX_S2_Фиксатор_трубок_подачи_пластика](./STL_Тюнинг/DX_S2_Фиксатор_трубок_подачи_пластика)

  * [DX_Вентиляторы_обдува_детали](./STL_Тюнинг/DX_Вентиляторы_обдува_детали)
  * [DX_Фиксатор_трубок_подачи_для_Формакс](./STL_Тюнинг/DX_Фиксатор_трубок_подачи_для_Формакс)

  * [DXL_DPXL_Крепление_стекла](./STL_Тюнинг/DXL_DPXL_Крепление_стекла)
  * [DXL_DPXL_Центровщик_флешки_для_принтера](./STL_Тюнинг/DXL_DPXL_Центровщик_флешки_для_принтера.stl)
  * [DXL_Воздухоотвод_для_принтера](./STL_Тюнинг/DXL_Воздухоотвод_для_принтера.stl)

  * [Контейнеры_для_мусора](./STL_Тюнинг/Контейнеры_для_мусора)
  * [Крепление_трубки_подачи](./STL_Тюнинг/Крепление_трубки_подачи)
  * [Кронштейн_для_катушки_0](./STL_Тюнинг/Кронштейн_для_катушки_0)
  * [Кронштейн_для_катушки_1](./STL_Тюнинг/Кронштейн_для_катушки_1)
  * [Кронштейн_для_катушки_3](./STL_Тюнинг/Кронштейн_для_катушки_3)
  * [Кронштейн_для_катушки_4](./STL_Тюнинг/Кронштейн_для_катушки_4)
  * [Фильтры_пыли](./STL_Тюнинг/Фильтры_пыли)

  * [Filament_tube_feeder](./STL_Тюнинг/Filament_tube_feeder.stl)
  * [Держатель_для_ключа_сопла](./STL_Тюнинг/Держатель_для_ключа_сопла.stl)

## Инструкции

### [Подшипники_S1](./Подшипники_S1)

### [Инструкции](./Инструкции)
  * [Builder_Picaso_инструкция.pdf](./Инструкции/Builder_Picaso_инструкция.pdf)

  * [DES_PRO250_Замена_ремней](./Инструкции/DES_PRO250_Замена_ремней)
  * [DES_PRO250_Ошибка_DEF_DEF.pdf](./Инструкции/DES_PRO250_Ошибка_DEF_DEF.pdf)
  * [DES_PRO250_Почему_не_подается_пластик.pdf](./Инструкции/DES_PRO250_Почему_не_подается_пластик.pdf)
  * [DES_PRO250_Сборка_нагревателя.pdf](./Инструкции/DES_PRO250_Сборка_нагревателя.pdf)
  * [DES_Замена_роликов_швеллер.pdf](./Инструкции/DES_Замена_роликов_швеллер.pdf)
  * [DES_Прочистка_трубки_нагревательного_элемента.pdf](./Инструкции/DES_Прочистка_трубки_нагревательного_элемента.pdf)
  * [PRO250_Калибровка_сопел_совмещение.pdf](./Инструкции/PRO250_Калибровка_сопел_совмещение.pdf)
  * [PRO250_Настройка_датчика_стола.pdf](./Инструкции/PRO250_Настройка_датчика_стола.pdf)
  * [PRO250_Проверка_напряжений_на_моторах.pdf](./Инструкции/PRO250_Проверка_напряжений_на_моторах.pdf)
  * [PRO250_Прочистка_нагревателя.pdf](./Инструкции/PRO250_Прочистка_нагревателя.pdf)
  * [PRO250_Разборка_головы.pdf](./Инструкции/PRO250_Разборка_головы.pdf)
  * [PRO250_Утилита_Service_exe_Калибровка_сопел_совмещение](./Инструкции/PRO250_Утилита_Service_exe_Калибровка_сопел_совмещение)

  * [X_Диагностика_блока_энкодеров.pdf](./Инструкции/X_Диагностика_блока_энкодеров.pdf)
  * [X_XPRO_Замена_заднего_крепления_стекла_.pdf](./Инструкции/X_XPRO_Замена_заднего_крепления_стекла_.pdf)
  * [X_XPRO_Настройка_стола.docx.pdf](./Инструкции/X_XPRO_Настройка_стола.docx.pdf)

  * [XPRO_Неполный_разбор_печатающей_головы.pdf](./Инструкции/XPRO_Неполный_разбор_печатающей_головы.pdf)
  * [XPRO_Проверка_замена_роликов_и_ремней.pdf](./Инструкции/XPRO_Проверка_замена_роликов_и_ремней.pdf)
  * [XPRO_Прочистка_нагревателя.pdf](./Инструкции/XPRO_Прочистка_нагревателя.pdf)
  * [XPRO_Список_ошибок.pdf](./Инструкции/XPRO_Список_ошибок.pdf)

  * [XL_XLPRO_Настройка_ШВП.pdf](./Инструкции/XL_XLPRO_Настройка_ШВП.pdf)

  * [Инструкция_по_упаковке_принтеров.pdf](./Инструкции/Инструкция_по_упаковке_принтеров.pdf)
  * [Инструкция_ШС_Шкаф_Сушильный.pdf](./Инструкции/Инструкция_ШС_Шкаф_Сушильный.pdf)

## Настройки слайсеров, профили пластиков

### [Cura](./_Cura)
  
### [S3D_для_Picaso_Статья_о_настройке](./_S3D_для_Picaso_Статья_о_настройке)

### [Профили_Polygon_XPRO](./Профили_пластиков_S3D_Polygon/Профили_Polygon_XPRO)

<details>
<summary>Список профилей для Polygon для XPRO</summary>

1. ABSM_PETG
1. BESTF_ABS
1. BESTF_PLA_BLACK
1. ESUN_ABS
1. ESUN_PLA_200
1. ESUN_PLA
1. FILM_CERAMO
1. FILM_SBS
1. FLEX_HARD PprintProduct
1. NYLON_MOD_PprintProduct
1. NYLON STRONG_PP
1. PICASO_ABS
1. PICASO_HIPS
1. PICASO_PLA
1. PICASO PVA(ESUN)
1. PICASO_PVA(REC)
1. PLA_PrintProduct
1. REC_ABS
1. REC_FLEX
1. REC_HIPS
1. REC_PLA
1. TAULMAN_910
1. U3PRINT_PC
1. VOLPRINT_PLA

</details>

### [Профили_Simplify3D](./Профили_пластиков_S3D_Polygon/Профили_Simplify3D)

<details>
<summary>Список профилей для Simplify3D для DPX, DX</summary>

1. all_profiles_DX_DXP.factory
1. Picaso_DPX_ABS-PA+HIPS_script.fff
1. Picaso_DPX_FlexHARD+PLA(F).fff
1. Picaso_DPX_F_WAX3D.fff
1. Picaso_DPX_GF4+HIPS_script.fff
1. Picaso_DPX_PETG(BF)+PLA(F).fff
1. Picaso_DPX_PETG+PLA(F)_script.fff
1. Picaso_DPX_PLA+PVA(eSUN).fff
1. Picaso_DPX_PLA+PVA(REC).fff
1. Picaso_DPX_TPU(A75)+PLA(F).fff
1. Picaso_DPX_TPU(A80)+PLA(F).fff
1. Picaso_DPX_TPU(A93)+PLA(F).fff
1. Picaso_DX_ABS_LITHOPANE.fff
1. Picaso_DX_BF_PLA.fff
1. Picaso_DX_CLOTHO-ABS-GF13.fff
1. Picaso_DX_eSUN_ePA-CF.fff
1. Picaso_DX_FD_TPU-A75.fff
1. Picaso_DX_F_ABS-PA-GF8.fff
1. Picaso_DX_F_ABS-PA.fff
1. Picaso_DX_F_ABS.fff
1. Picaso_DX_F_CERAMO.fff
1. Picaso_DX_F_GF4.fff
1. Picaso_DX_F_PA66-GF30.fff
1. Picaso_DX_F_PBT-GF30.fff
1. Picaso_DX_F_PETg.fff
1. Picaso_DX_F_PLA.fff
1. Picaso_DX_F_PP-GF30.fff
1. Picaso_DX_F_PP.fff
1. Picaso_DX_F_PRO-FLEX.fff
1. Picaso_DX_F_SBS.fff
1. Picaso_DX_F_TERMAX-GF40.fff
1. Picaso_DX_F_TITAN_ABS-GF12.fff
1. Picaso_DX_F_TPU-A80.fff
1. Picaso_DX_F_TPU-A93.fff
1. Picaso_DX_F_TPU-CF5.fff
1. Picaso_DX_F_TPU-GF10.fff
1. Picaso_DX_F_TPU-GF30.fff
1. Picaso_DX_HTP_NYLON.fff
1. Picaso_DX_IGUS_J260.fff
1. Picaso_DX_PrPr_FlexHARD.fff
1. Picaso_DX_REC_FORMAX.fff
1. Picaso_DX_REC_RUBBER.fff
1. Picaso_DX_REC_TPU-D70.fff

</details>

### [Профили_Simplify_PRO250](./Профили_пластиков_S3D_Polygon/Профили_Simplify_PRO250)

<details>
<summary>Список профилей для Simplify3D для PRO250</summary>

1. Picaso ABS 0.8.fff
1. PICASO ABS 2 heads support dens.fff
1. Picaso Designer PRO250.fff
1. PICASO DUAL COLOR.fff
1. PRO250 ABS 0.3 color_A.fff
1. PRO250 ABS 0.3 color_B.fff
1. PRO250 ABS 1 head 0.3.fff
1. PRO250 ABS_HIPS 2hds 85dens.fff
1. PRO250 ABS_PC 0.3 1extruder.fff
1. PRO250 SBS 0.8 transparent-Bottle Small.fff
1. PRO250 SBS 0.8 transparent-Bottle.fff

</details>

## Ремонт, тюнинг

### [Сопливчик_форма_для_литья](./Сопливчик_форма_для_литья)

### [Стёкла](./Стёкла)
   * [250PRO_стекло_0.jpg](./Стёкла/img/250PRO_стекло_0.jpg)
   * [250PRO_стекло_1.jpg](./Стёкла/img/250PRO_стекло_1.jpg)
   * [XPRO_Стекло_0.jpg](./Стёкла/img/XPRO_Стекло_0.jpg)
   * [XPRO_Стекло_1.jpg](./Стёкла/img/XPRO_Стекло_1.jpg)
   * [PicasoXL_glass_template_v8](./Стёкла/PicasoXL_glass_template_v8.stl)
   * [XL_glass.pdf](./Стёкла/XL_glass.pdf)

## Справочное

### [Сушка_пластика](./Сушка_пластика)
  
### [Термопаста_смазки (uc)](./Термопаста_смазки (uc))
   
### [Размеры_масса_катушек_филамента.xlsx](./Размеры_масса_катушек_филамента.xlsx)

## Разное

### [Картонная_катушка_HTP](./Картонная_катушка_HTP)

### [Листы_PEI](./Листы_PEI)

### [Несортированное](./Несортированное)

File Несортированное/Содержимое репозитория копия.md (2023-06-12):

# Содержимое репозитория:

## [Firmware (Фотографии плат, покупные радиоэлементы)](./Firmware)

  * [DES](.\Picaso3D\Firmware\DES_Firmware)
  * [DPXL](.\Picaso3D\Firmware\DPXL_Firmware)
    * [XLPRO_XPRO_Мотор_переключения_сопел](.\Picaso3D\Firmware\DPXL_Firmware\XLPRO_XPRO_Мотор_переключения_сопел.lnk)
  * [DPX](.\Picaso3D\Firmware\DPX_Firmware_(under_construction))
    * [DPX_DPXL_Мотор_переключения_сопел](.\Picaso3D\Firmware\DPX_Firmware_(under_construction)\DPX_DPXL_Мотор_переключения_сопел)
    * [DPX_Electronic_components](.\Picaso3D\Firmware\DPX_Firmware_(under_construction)\DPX_Electronic_components)
    * [DPX_Motherboard](.\Picaso3D\Firmware\DPX_Firmware_(under_construction)\DPX_Motherboard)
    * [DPX_Ремень](.\Picaso3D\Firmware\DPX_Firmware_(under_construction)\DPX_Ремень)
    * [DPX_Энкодер](.\Picaso3D\Firmware\DPX_Firmware_(under_construction)\DPX_Энкодер)
  * [DPX_S2](.\Picaso3D\Firmware\DPX_S2_Firmware)
  * [DXL_S2](.\Picaso3D\Firmware\DXL_S2_Firmware)
  * [DX](.\Picaso3D\Firmware\DX_Firmware_(under_construction))
  * [DX_S2](.\Picaso3D\Firmware\DX_S2_Firmware)
  * [PRO250](.\Picaso3D\Firmware\PRO250_Firmware)
  * [Покупные_радиоэлементы_разное](.\Picaso3D\Firmware\Покупные_радиоэлементы_разное)
    * [Муфта](.\Picaso3D\Firmware\Покупные_радиоэлементы_разное\Муфта)
    * [Ссылки](.\Picaso3D\Firmware\Покупные_радиоэлементы_разное\Ссылки)
    * [Фотографии](.\Picaso3D\Firmware\Покупные_радиоэлементы_разное\Фотографии)

## [Software (Программное обеспечение, прошивки)](.\Picaso3D\Software)

  * [PRO250_EEPROM](.\Picaso3D\Software\PRO250_EEPROM (uc))
  * [PRO250_Прошивки](.\Picaso3D\Software\PRO250_Прошивки)
  * [DES_Klipper_cfg](.\Picaso3D\Software\DES_Klipper_cfg)
  * [DES_Marlin_cfg](.\Picaso3D\Software\DES_Marlin_cfg)
  * [XPRO_Прошивки](.\Picaso3D\Software\XPRO_Прошивки)
  * [PolygonX](.\Picaso3D\Software\PolygonX)

## STL-файлы для ремонта принтера, тюнинга, файлы для калибровки

### [STL_Детали_принтеров](.\Picaso3D\STL_Детали_принтеров)

   * [PRO250](.\Picaso3D\STL_Детали_принтеров\PRO250)
     * [PRO250_HolderUpgrade](.\Picaso3D\STL_Детали_принтеров\PRO250\PRO250_HolderUpgrade)
     * [PRO250_Filament_Feeder](.\Picaso3D\STL_Детали_принтеров\PRO250\PRO250_Filament_Feeder.stl)
     * [PRO250_Y_endstop](.\Picaso3D\STL_Детали_принтеров\PRO250\PRO250_Y_endstop.stl)
     * [PRO250_Y_Shaft_holder](.\Picaso3D\STL_Детали_принтеров\PRO250\PRO250_Y_Shaft_holder.stl)
     * [PRO250_Кронштейн](.\Picaso3D\STL_Детали_принтеров\PRO250\PRO250_Кронштейн.stl)
     * [PRO250_Крутилка_стола](.\Picaso3D\STL_Детали_принтеров\PRO250\PRO250_Крутилка_стола.stl)
     * [PRO250_Сборка_головы](.\Picaso3D\STL_Детали_принтеров\PRO250\PRO250_Сборка_головы.stp)
     * [PRO250_Центральная_шестерня.pdf](.\Picaso3D\STL_Детали_принтеров\PRO250\PRO250_Центральная_шестерня.pdf)
     * [DPS_004.10.08_Филамент](.\Picaso3D\STL_Детали_принтеров\PRO250\DPS_004.10.08_Филамент.stl)
     * [Держатель_очистителя_PRO250_под_очиститель_X_PRO_repaired_fixed](.\Picaso3D\STL_Детали_принтеров\PRO250\Держатель_очистителя_PRO250_под_очиститель_X_PRO_repaired_fixed.stl)
     * [Контейнер_под_держатель_чистика](.\Picaso3D\STL_Детали_принтеров\PRO250\Контейнер_под_держатель_чистика.stl)
     * [Упор_концевика](.\Picaso3D\STL_Детали_принтеров\PRO250\Упор_концевика.stl)
     * [Шайба_двигателя_переключения_сопел](.\Picaso3D\STL_Детали_принтеров\PRO250\Шайба_двигателя_переключения_сопел.stl)
  
  * [DES_Кронштейн](.\Picaso3D\STL_Детали_принтеров\DES_Кронштейн.stl)
  * [DES_Проставка_экструдер](.\Picaso3D\STL_Детали_принтеров\DES_Проставка_экструдер.stl)

  * [DESС_00.00.03_Петля_верхняя_скрытая](.\Picaso3D\STL_Детали_принтеров\DESС_00.00.03_Петля_верхняя_скрытая.stl)
  * [DESС_00.00.04_Петля_нижняя_скрытая](.\Picaso3D\STL_Детали_принтеров\DESС_00.00.04_Петля_нижняя_скрытая.stl)
  * [DESС_00.00.06_Петля_средняя_скрытая](.\Picaso3D\STL_Детали_принтеров\DESС_00.00.06_Петля_средняя_скрытая.stl)

  * [DPS_004.10.08_Филамент](.\Picaso3D\STL_Детали_принтеров\DPS_004.10.08_Филамент.stl)
  * [DPS_004.10.09_Держатель_трубок](.\Picaso3D\STL_Детали_принтеров\DPS_004.10.09_Держатель_трубок.stl)
  * [DPS_01.00.14_Левый_зажим_эксцентрик](.\Picaso3D\STL_Детали_принтеров\DPS_01.00.14_Левый_зажим_эксцентрик.stl)
  * [DPS_01.00.14_Правый_зажим_эксцентрик.](.\Picaso3D\STL_Детали_принтеров\DPS_01.00.14_Правый_зажим_эксцентрик.stl)
  * [DPS_02.00.02_01_Стойка_для_валов_XY](.\Picaso3D\STL_Детали_принтеров\DPS_02.00.02_01_Стойка_для_валов_XY.stl)
  * [DPS_02.00.08.01_Держатель_трубки](.\Picaso3D\STL_Детали_принтеров\DPS_02.00.08.01_Держатель_трубки.stl)
  * [DPS_02.00.08_01_Держатель_трубки_](.\Picaso3D\STL_Детали_принтеров\DPS_02.00.08_01_Держатель_трубки_.stl)
  * [DPS_02.00.09_Держатель_чистика](.\Picaso3D\STL_Детали_принтеров\DPS_02.00.09_Держатель_чистика.stl)

  * [DEX_Фиксатор_трубки_подачи_пластика](.\Picaso3D\STL_Детали_принтеров\DEX_Фиксатор_трубки_подачи_пластика.stl)  
  * [DPX_00.00.05_Держатель_катушки](.\Picaso3D\STL_Детали_принтеров\DPX_00.00.05_Держатель_катушки.stl)
  * [DPX_02.00.02_Держатель_роликов_левый](.\Picaso3D\STL_Детали_принтеров\DPX_02.00.02_Держатель_роликов_левый.stl)
  * [DPX_02.00.03_Держатель_роликов_правый](.\Picaso3D\STL_Детали_принтеров\DPX_02.00.03_Держатель_роликов_правый.stl)
  * [DPX_02.00.04_Втулка_правого_держателя](.\Picaso3D\STL_Детали_принтеров\DPX_02.00.04_Втулка_правого_держателя.stl)
  * [DPX_02.00.05_Втулка_дистанционная_new](.\Picaso3D\STL_Детали_принтеров\DPX_02.00.05_Втулка_дистанционная_new.stl)
  * [DPX_02.00.16_Держатель_чистика_V1](.\Picaso3D\STL_Детали_принтеров\DPX_02.00.16_Держатель_чистика_V1.stl)
  * [DPX_04.00.03_Крутилка](.\Picaso3D\STL_Детали_принтеров\DPX_04.00.03_Крутилка.stl)
  * [DPX_Держатель_пружины](.\Picaso3D\STL_Детали_принтеров\DPX_Держатель_пружины.stl)
  * [DPX_Держатель_трубки_v1](.\Picaso3D\STL_Детали_принтеров\DPX_Держатель_трубки_v1.stl)
  * [DPX_Фиксатор_трубок_подачи_пластика](.\Picaso3D\STL_Детали_принтеров\DPX_Фиксатор_трубок_подачи_пластика.stl)
  * [DPX_Чистик](.\Picaso3D\STL_Детали_принтеров\DPX_Чистик.stl)
  * [DPX_Блоки_энкодеров_S1_S2](.\Picaso3D\STL_Детали_принтеров\DPX_Блоки_энкодеров_S1_S2)
  * [DPX_Направляющая_трубки_подачи_пластика](.\Picaso3D\STL_Детали_принтеров\DPX_Направляющая_трубки_подачи_пластика)

  * [DXL_DPXL_Боковой_фиксатор_трубки_подачи_пластика](.\Picaso3D\STL_Детали_принтеров\DXL_DPXL_Боковой_фиксатор_трубки_подачи_пластика.stl)
  * [DXL_Воздуховод](.\Picaso3D\STL_Детали_принтеров\DXL_Воздуховод.stl)
  * [DXL_Воздуховод_short](.\Picaso3D\STL_Детали_принтеров\DXL_Воздуховод_short.stl)
  * [DXL_Заглушка](.\Picaso3D\STL_Детали_принтеров\DXL_Заглушка.stl)
  * [DXL_Фиксатор_винта_М4](.\Picaso3D\STL_Детали_принтеров\DXL_Фиксатор_винта_М4.stl)
  * [DXL_Блок_энкодера](.\Picaso3D\STL_Детали_принтеров\DXL_Блок_энкодера)
  * [DPXL_Фиксатор_прижимного_винта_М4.](.\Picaso3D\STL_Детали_принтеров\DPXL_Фиксатор_прижимного_винта_М4.stl)

  * [DX_02.00.09_Держатель_чистика.](.\Picaso3D\STL_Детали_принтеров\DX_02.00.09_Держатель_чистика.stl)
  * [DX_radfan_v1.0](.\Picaso3D\STL_Детали_принтеров\DX_radfan_v1.0.stl)
  * [DX_Держатель_прижимной_пружины](.\Picaso3D\STL_Детали_принтеров\DX_Держатель_прижимной_пружины.stl)
  * [DX_Держатель_пружины](.\Picaso3D\STL_Детали_принтеров\DX_Держатель_пружины.stl)
  * [DX_Блок_энкодера_Корпус](.\Picaso3D\STL_Детали_принтеров\DX_Блок_энкодера_Корпус)
  * [DX_Проставка_радиатора](.\Picaso3D\STL_Детали_принтеров\DX_Проставка_радиатора)

  * [Воздуховод](.\Picaso3D\STL_Детали_принтеров\Воздуховод.stl)
  * [Деталь_филамента](.\Picaso3D\STL_Детали_принтеров\Деталь_филамента.stl)
  * [Кронштейн_для_кабель_канала](.\Picaso3D\STL_Детали_принтеров\Кронштейн_для_кабель_канала.stl)
  * [Петля_в_сборе](.\Picaso3D\STL_Детали_принтеров\Петля_в_сборе.stl)
  * [Сухари](.\Picaso3D\STL_Детали_принтеров\Сухари)
  * [Шайба_двигателя_переключения_сопел](.\Picaso3D\STL_Детали_принтеров\Шайба_двигателя_переключения_сопел.stl)
  * [Шайба_двигателя_переключения_сопел](.\Picaso3D\STL_Детали_принтеров\Шайба_двигателя_переключения_сопел) 

### [STL_Калибровочные_шаблоны](.\Picaso3D\STL_Калибровочные_шаблоны)
 
  * [PRO250_Сведение_сопел](.\Picaso3D\STL_Калибровочные_шаблоны\PRO250_Сведение_сопел)
  * [PRO250_Тест_ремней](.\Picaso3D\STL_Калибровочные_шаблоны\PRO250_Тест_ремней)
  * [Калибровочный_шаблон_очистителя](.\Picaso3D\STL_Калибровочные_шаблоны\Калибровочный_шаблон_очистителя.stl)
  * [Калибровочный_шаблон_очистителя_0XYn](.\Picaso3D\STL_Калибровочные_шаблоны\Калибровочный_шаблон_очистителя_0XYn.stl)
  * [Калибровочный_шаблон_очистителя_XY0.plgx](.\Picaso3D\STL_Калибровочные_шаблоны\Калибровочный_шаблон_очистителя_XY0.plgx)
  * [Настройка_прижима](.\Picaso3D\STL_Калибровочные_шаблоны\Настройка_прижима.stl)
  * [Настройка_прижима_200x200](.\Picaso3D\STL_Калибровочные_шаблоны\Настройка_прижима_200x200.stl)
  * [Настройка_прижима_куб_2х2х2](.\Picaso3D\STL_Калибровочные_шаблоны\Настройка_прижима_куб_2х2х2.stl)
  * [Настройка_прижима_ХPRO_0.25.plgx](.\Picaso3D\STL_Калибровочные_шаблоны\Настройка_прижима_ХPRO_0.25.plgx)
  * [Сведение_сопел_0.3.plgx](.\Picaso3D\STL_Калибровочные_шаблоны\Сведение_сопел_0.3.plgx)
  * [Сведение_сопел_ABS.plg](.\Picaso3D\STL_Калибровочные_шаблоны\Сведение_сопел_ABS.plg)
  * [Сведение_сопел_PLA.plg](.\Picaso3D\STL_Калибровочные_шаблоны\Сведение_сопел_PLA.plg)
  * [Сведение_сопел_грубо.plgx](.\Picaso3D\STL_Калибровочные_шаблоны\Сведение_сопел_грубо.plgx)
  * [Сведение_сопел_грубо_полный.plgx](.\Picaso3D\STL_Калибровочные_шаблоны\Сведение_сопел_грубо_полный.plgx)
  * [Сведение_сопел_кольца_0_25_0_5.plgx](.\Picaso3D\STL_Калибровочные_шаблоны\Сведение_сопел_кольца_0_25_0_5.plgx)

### [STL_Тюнинг](.\Picaso3D\STL_Тюнинг)
 
  * [DPXL_Фиксатор_трубок_подачи_пластика](.\Picaso3D\STL_Тюнинг\DPXL_Фиксатор_трубок_подачи_пластика)
  * [DPX_Фиксатор_трубок_подачи_пластика_mod3](.\Picaso3D\STL_Тюнинг\DPX_Фиксатор_трубок_подачи_пластика_mod3)

  * [DX_S2_Фиксатор_трубок_подачи_пластика](.\Picaso3D\STL_Тюнинг\DX_S2_Фиксатор_трубок_подачи_пластика)

  * [DX_Вентиляторы_обдува_детали](.\Picaso3D\STL_Тюнинг\DX_Вентиляторы_обдува_детали)
  * [DX_Фиксатор_трубок_подачи_для_Формакс](.\Picaso3D\STL_Тюнинг\DX_Фиксатор_трубок_подачи_для_Формакс)

  * [DXL_DPXL_Крепление_стекла](.\Picaso3D\STL_Тюнинг\DXL_DPXL_Крепление_стекла)
  * [DXL_DPXL_Центровщик_флешки_для_принтера](.\Picaso3D\STL_Тюнинг\DXL_DPXL_Центровщик_флешки_для_принтера.stl)
  * [DXL_Воздухоотвод_для_принтера](.\Picaso3D\STL_Тюнинг\DXL_Воздухоотвод_для_принтера.stl)

  * [Контейнеры_для_мусора](.\Picaso3D\STL_Тюнинг\Контейнеры_для_мусора)
  * [Крепление_трубки_подачи](.\Picaso3D\STL_Тюнинг\Крепление_трубки_подачи)
  * [Кронштейн_для_катушки_0](.\Picaso3D\STL_Тюнинг\Кронштейн_для_катушки_0)
  * [Кронштейн_для_катушки_1](.\Picaso3D\STL_Тюнинг\Кронштейн_для_катушки_1)
  * [Кронштейн_для_катушки_3](.\Picaso3D\STL_Тюнинг\Кронштейн_для_катушки_3)
  * [Кронштейн_для_катушки_4](.\Picaso3D\STL_Тюнинг\Кронштейн_для_катушки_4)
  * [Фильтры_пыли](.\Picaso3D\STL_Тюнинг\Фильтры_пыли)

  * [Filament_tube_feeder](.\Picaso3D\STL_Тюнинг\Filament_tube_feeder.stl)
  * [Держатель_для_ключа_сопла](.\Picaso3D\STL_Тюнинг\Держатель_для_ключа_сопла.stl)

## Инструкции

### [Подшипники_S1](.\Picaso3D\Подшипники_S1)

### [Инструкции](.\Picaso3D\Инструкции)
  * [Builder_Picaso_инструкция.pdf](.\Picaso3D\Инструкции\Builder_Picaso_инструкция.pdf)

  * [DES_PRO250_Замена_ремней](.\Picaso3D\Инструкции\DES_PRO250_Замена_ремней)
  * [DES_PRO250_Ошибка_DEF_DEF.pdf](.\Picaso3D\Инструкции\DES_PRO250_Ошибка_DEF_DEF.pdf)
  * [DES_PRO250_Почему_не_подается_пластик.pdf](.\Picaso3D\Инструкции\DES_PRO250_Почему_не_подается_пластик.pdf)
  * [DES_PRO250_Сборка_нагревателя.pdf](.\Picaso3D\Инструкции\DES_PRO250_Сборка_нагревателя.pdf)
  * [DES_Замена_роликов_швеллер.pdf](.\Picaso3D\Инструкции\DES_Замена_роликов_швеллер.pdf)
  * [DES_Прочистка_трубки_нагревательного_элемента.pdf](.\Picaso3D\Инструкции\DES_Прочистка_трубки_нагревательного_элемента.pdf)
  * [PRO250_Калибровка_сопел_совмещение.pdf](.\Picaso3D\Инструкции\PRO250_Калибровка_сопел_совмещение.pdf)
  * [PRO250_Настройка_датчика_стола.pdf](.\Picaso3D\Инструкции\PRO250_Настройка_датчика_стола.pdf)
  * [PRO250_Проверка_напряжений_на_моторах.pdf](.\Picaso3D\Инструкции\PRO250_Проверка_напряжений_на_моторах.pdf)
  * [PRO250_Прочистка_нагревателя.pdf](.\Picaso3D\Инструкции\PRO250_Прочистка_нагревателя.pdf)
  * [PRO250_Разборка_головы.pdf](.\Picaso3D\Инструкции\PRO250_Разборка_головы.pdf)
  * [PRO250_Утилита_Service_exe_Калибровка_сопел_совмещение](.\Picaso3D\Инструкции\PRO250_Утилита_Service_exe_Калибровка_сопел_совмещение)

  * [X_Диагностика_блока_энкодеров.pdf](.\Picaso3D\Инструкции\X_Диагностика_блока_энкодеров.pdf)
  * [X_XPRO_Замена_заднего_крепления_стекла_.pdf](.\Picaso3D\Инструкции\X_XPRO_Замена_заднего_крепления_стекла_.pdf)
  * [X_XPRO_Настройка_стола.docx.pdf](.\Picaso3D\Инструкции\X_XPRO_Настройка_стола.docx.pdf)

  * [XPRO_Неполный_разбор_печатающей_головы.pdf](.\Picaso3D\Инструкции\XPRO_Неполный_разбор_печатающей_головы.pdf)
  * [XPRO_Проверка_замена_роликов_и_ремней.pdf](.\Picaso3D\Инструкции\XPRO_Проверка_замена_роликов_и_ремней.pdf)
  * [XPRO_Прочистка_нагревателя.pdf](.\Picaso3D\Инструкции\XPRO_Прочистка_нагревателя.pdf)
  * [XPRO_Список_ошибок.pdf](.\Picaso3D\Инструкции\XPRO_Список_ошибок.pdf)

  * [XL_XLPRO_Настройка_ШВП.pdf](.\Picaso3D\Инструкции\XL_XLPRO_Настройка_ШВП.pdf)

  * [Инструкция_по_упаковке_принтеров.pdf](.\Picaso3D\Инструкции\Инструкция_по_упаковке_принтеров.pdf)
  * [Инструкция_ШС_Шкаф_Сушильный.pdf](.\Picaso3D\Инструкции\Инструкция_ШС_Шкаф_Сушильный.pdf)

## Настройки слайсеров, профили пластиков

### [Cura](.\Picaso3D\_Cura)
  
### [S3D_для_Picaso_Статья_о_настройке](.\Picaso3D\_S3D_для_Picaso_Статья_о_настройке)

### [Профили_Polygon_XPRO](.\Picaso3D\Профили_пластиков_S3D_Polygon\Профили_Polygon_XPRO)

<details>
<summary>Список профилей для Polygon для XPRO</summary>

1. ABSM_PETG
1. BESTF_ABS
1. BESTF_PLA_BLACK
1. ESUN_ABS
1. ESUN_PLA_200
1. ESUN_PLA
1. FILM_CERAMO
1. FILM_SBS
1. FLEX_HARD PprintProduct
1. NYLON_MOD_PprintProduct
1. NYLON STRONG_PP
1. PICASO_ABS
1. PICASO_HIPS
1. PICASO_PLA
1. PICASO PVA(ESUN)
1. PICASO_PVA(REC)
1. PLA_PrintProduct
1. REC_ABS
1. REC_FLEX
1. REC_HIPS
1. REC_PLA
1. TAULMAN_910
1. U3PRINT_PC
1. VOLPRINT_PLA

</details>

### [Профили_Simplify3D](.\Picaso3D\Профили_пластиков_S3D_Polygon\Профили_Simplify3D)

<details>
<summary>Список профилей для Simplify3D для DPX, DX</summary>

1. all_profiles_DX_DXP.factory
1. Picaso_DPX_ABS-PA+HIPS_script.fff
1. Picaso_DPX_FlexHARD+PLA(F).fff
1. Picaso_DPX_F_WAX3D.fff
1. Picaso_DPX_GF4+HIPS_script.fff
1. Picaso_DPX_PETG(BF)+PLA(F).fff
1. Picaso_DPX_PETG+PLA(F)_script.fff
1. Picaso_DPX_PLA+PVA(eSUN).fff
1. Picaso_DPX_PLA+PVA(REC).fff
1. Picaso_DPX_TPU(A75)+PLA(F).fff
1. Picaso_DPX_TPU(A80)+PLA(F).fff
1. Picaso_DPX_TPU(A93)+PLA(F).fff
1. Picaso_DX_ABS_LITHOPANE.fff
1. Picaso_DX_BF_PLA.fff
1. Picaso_DX_CLOTHO-ABS-GF13.fff
1. Picaso_DX_eSUN_ePA-CF.fff
1. Picaso_DX_FD_TPU-A75.fff
1. Picaso_DX_F_ABS-PA-GF8.fff
1. Picaso_DX_F_ABS-PA.fff
1. Picaso_DX_F_ABS.fff
1. Picaso_DX_F_CERAMO.fff
1. Picaso_DX_F_GF4.fff
1. Picaso_DX_F_PA66-GF30.fff
1. Picaso_DX_F_PBT-GF30.fff
1. Picaso_DX_F_PETg.fff
1. Picaso_DX_F_PLA.fff
1. Picaso_DX_F_PP-GF30.fff
1. Picaso_DX_F_PP.fff
1. Picaso_DX_F_PRO-FLEX.fff
1. Picaso_DX_F_SBS.fff
1. Picaso_DX_F_TERMAX-GF40.fff
1. Picaso_DX_F_TITAN_ABS-GF12.fff
1. Picaso_DX_F_TPU-A80.fff
1. Picaso_DX_F_TPU-A93.fff
1. Picaso_DX_F_TPU-CF5.fff
1. Picaso_DX_F_TPU-GF10.fff
1. Picaso_DX_F_TPU-GF30.fff
1. Picaso_DX_HTP_NYLON.fff
1. Picaso_DX_IGUS_J260.fff
1. Picaso_DX_PrPr_FlexHARD.fff
1. Picaso_DX_REC_FORMAX.fff
1. Picaso_DX_REC_RUBBER.fff
1. Picaso_DX_REC_TPU-D70.fff

</details>

### [Профили_Simplify_PRO250](.\Picaso3D\Профили_пластиков_S3D_Polygon\Профили_Simplify_PRO250)

<details>
<summary>Список профилей для Simplify3D для PRO250</summary>

1. Picaso ABS 0.8.fff
1. PICASO ABS 2 heads support dens.fff
1. Picaso Designer PRO250.fff
1. PICASO DUAL COLOR.fff
1. PRO250 ABS 0.3 color_A.fff
1. PRO250 ABS 0.3 color_B.fff
1. PRO250 ABS 1 head 0.3.fff
1. PRO250 ABS_HIPS 2hds 85dens.fff
1. PRO250 ABS_PC 0.3 1extruder.fff
1. PRO250 SBS 0.8 transparent-Bottle Small.fff
1. PRO250 SBS 0.8 transparent-Bottle.fff

</details>

## Ремонт, тюнинг

### [Сопливчик_форма_для_литья](.\Picaso3D\Сопливчик_форма_для_литья)

### [Стёкла](.\Picaso3D\Стёкла)
   * [250PRO_стекло_0.jpg](.\Picaso3D\Стёкла\img\250PRO_стекло_0.jpg)
   * [250PRO_стекло_1.jpg](.\Picaso3D\Стёкла\img\250PRO_стекло_1.jpg)
   * [XPRO_Стекло_0.jpg](.\Picaso3D\Стёкла\img\XPRO_Стекло_0.jpg)
   * [XPRO_Стекло_1.jpg](.\Picaso3D\Стёкла\img\XPRO_Стекло_1.jpg)
   * [PicasoXL_glass_template_v8](.\Picaso3D\Стёкла\PicasoXL_glass_template_v8.stl)
   * [XL_glass.pdf](.\Picaso3D\Стёкла\XL_glass.pdf)

## Справочное

### [Сушка_пластика](.\Picaso3D\Сушка_пластика)
  
### [Термопаста_смазки (uc)](.\Picaso3D\Термопаста_смазки (uc))
   
### [Размеры_масса_катушек_филамента.xlsx](.\Picaso3D\Размеры_масса_катушек_филамента.xlsx)

## Разное

### [Картонная_катушка_HTP](.\Picaso3D\Картонная_катушка_HTP)

### [Листы_PEI](.\Picaso3D\Листы_PEI)

### [Несортированное](.\Picaso3D\Несортированное)

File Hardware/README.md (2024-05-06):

# Hardware/железо принтеров Picaso

В данном разделе хранятся:

+ фотографии плат управления принтеров Picaso;

+ радиоэлементы, используемые в принтерах (фотографии, ссылки на покупку, даташиты);

+ прочее, связанное с аппаратным обеспечением принтеров.

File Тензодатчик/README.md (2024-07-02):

# Тензодатчик для Picaso XL и XL PRO

1. Чтобы диагностировать работоспособность тензодатчика нужно проверить напряжение смещения, оно должно быть около 0 мВ, а если измеренное значение больше 0,75 мВ - то значит тензодатчик неисправен. Чтобы измерить это напряжение необходимо:

* выключить принтер,
* снять полностью тензодатчик,
* из разъема от тензодатчика вынуть зеленый и белый провода,
* разъем с подключенными красным и черным проводом подключить обратно к плате принтера,
* включить принтер,
* мультиметром в режиме измерения постоянного напряжения проконтролировать напряжение между белым и зеленым проводами. Оно должно быть близким к 0 мВ (не более 0,75 мВ).

> Возможно обойтись без принтера, подав 5 В с помощью внешнего источника питания.

2. Если датчик работоспособен, то установить его согласно инструкции. Пластина должна стоять со стороны 2-х винтов. 

> Совет: есть ключевой нюанс в установке, при котором тензодатчик будет выдавать неверные значения: после того как закрутили все винты и пока не схватился фиксатор, нужно тот винт, который ставится на фиксатор резьбы, выкрутить ровно на один оборот,. Только при такой установке можно поймать регулировочным винтом (который на стойке с пружиной) нужные значение напряжения тензодатчика в свободном положении от 1 до 2 В. У меня обычно около 1,6-1,7 В. Это напряжение нужно подкручивать до такого значения, чтобы при любом нажатии в нагревательный блок снизу напряжение становилось 3,27 В, а при нажатии на каретку от себя – где-то 0,128 В. При таком раскладе все будет работать корректно.

<p float="centr">
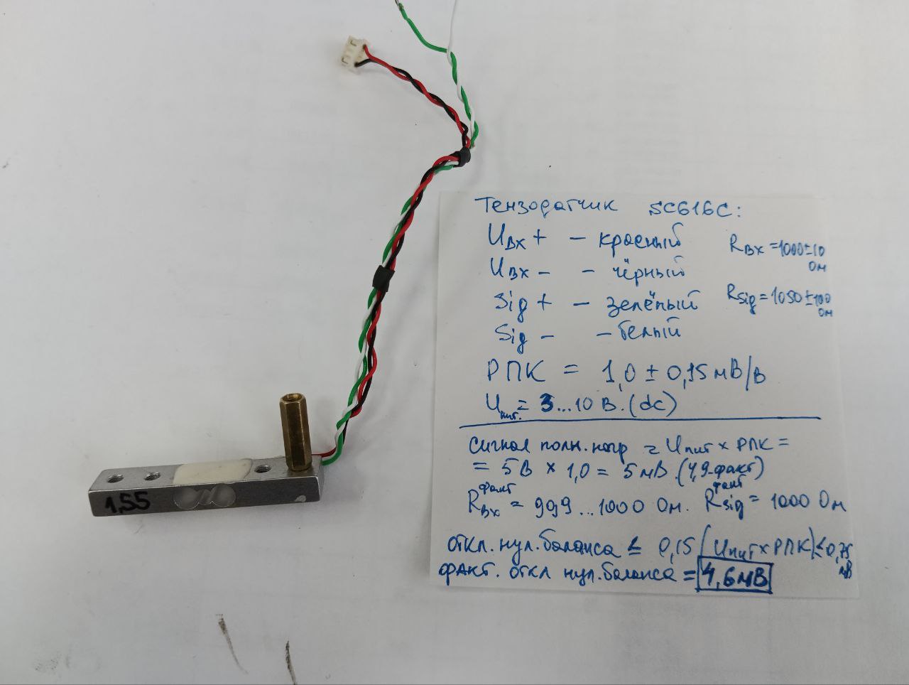
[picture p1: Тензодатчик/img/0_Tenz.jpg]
Тензодатчик
  
</p>

<picture><source media="(prefers-color-scheme: dark)" srcset="https://cdn.simpleicons.org/telegram/white"> <source media="(prefers-color-scheme: light)" srcset="https://cdn.simpleicons.org/telegram/black"> Telegram</picture> [Источник](https://t.me/Picaso3dUnofficial/321823)

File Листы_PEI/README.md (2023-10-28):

# Листы PEI для принтеров Picaso

Магнитная подложка для листа PEI клеится на стекло.

Лист PEI можно отпилить болгаркой, если не получится заказать нужный размер. Также можно спросить у продавца с Aliexpress - возможно, по заказу получится изготовить требуемый размер.

Ссылки для покупки:

1. https://sl.aliexpress.ru/p?key=HfHnxVD

1. https://a.aliexpress.com/_99EtPr

1. Лист PEI 377x370 мм: https://item.taobao.com/item.htm?spm=a1z0d.6639537/tb.1997196601.14.4ecc7484fJOoKn&id=652817769134

1. https://aliexpress.ru/item/1005004136943802.html

<p float="left">
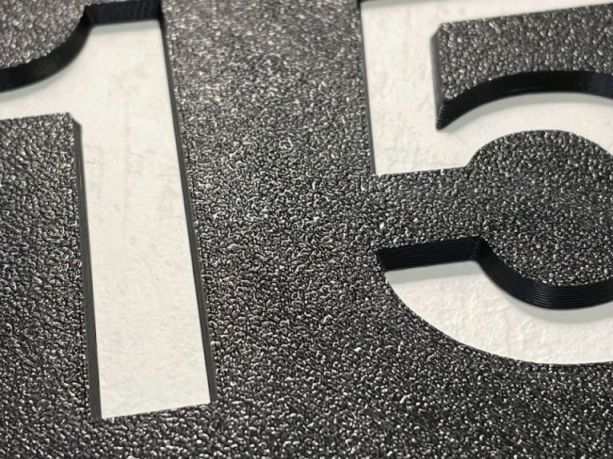
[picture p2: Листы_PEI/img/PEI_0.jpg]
PEI_0
  
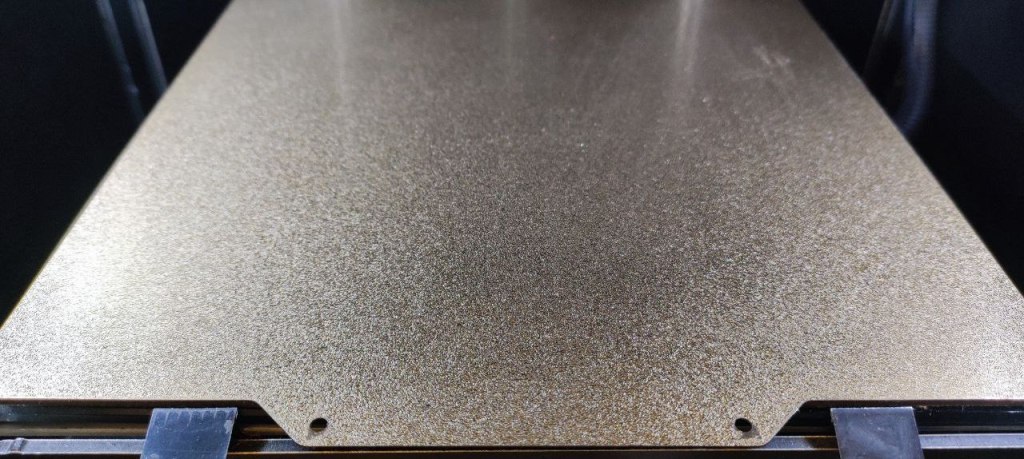
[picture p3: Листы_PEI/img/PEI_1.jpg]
PEI_1
  
</p>

<p float="left">
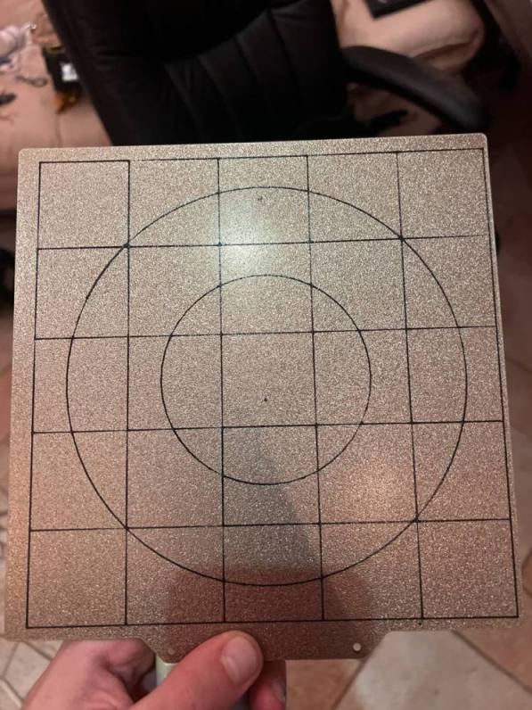
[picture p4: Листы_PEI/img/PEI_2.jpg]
PEI_2
  
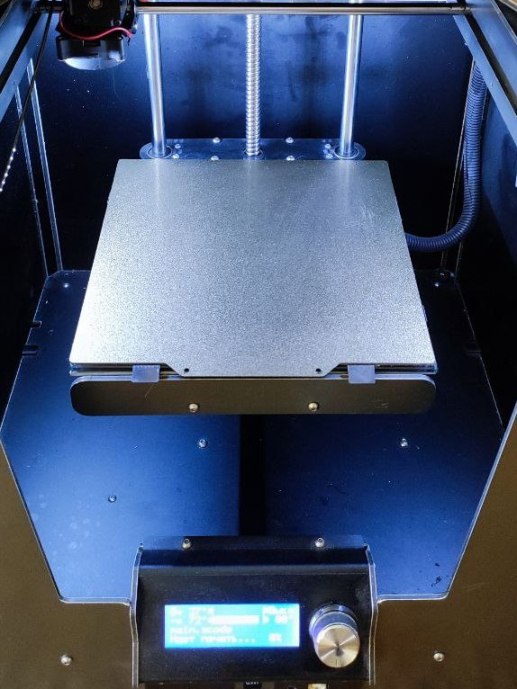
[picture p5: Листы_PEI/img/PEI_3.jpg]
PEI_3
  
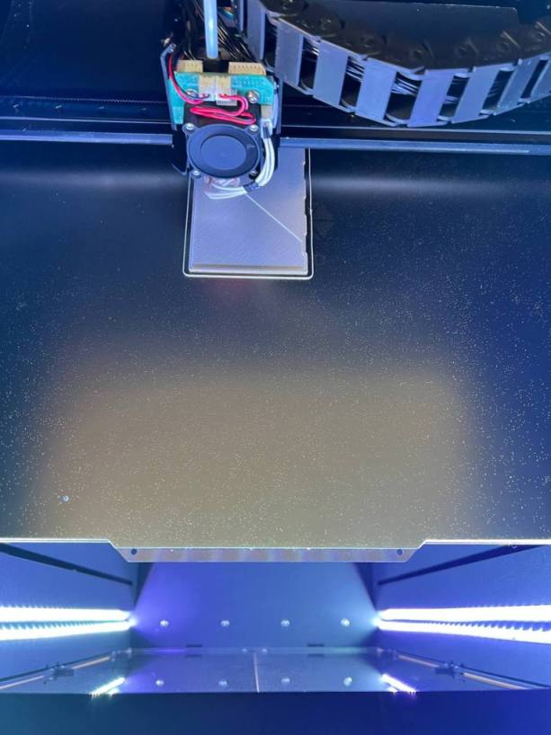
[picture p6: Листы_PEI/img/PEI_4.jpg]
PEI_4
  
</p>

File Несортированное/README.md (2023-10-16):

# Несортированное

1. DES_X_XPRO_XL_XLPRO_Термобарьер_из_чата
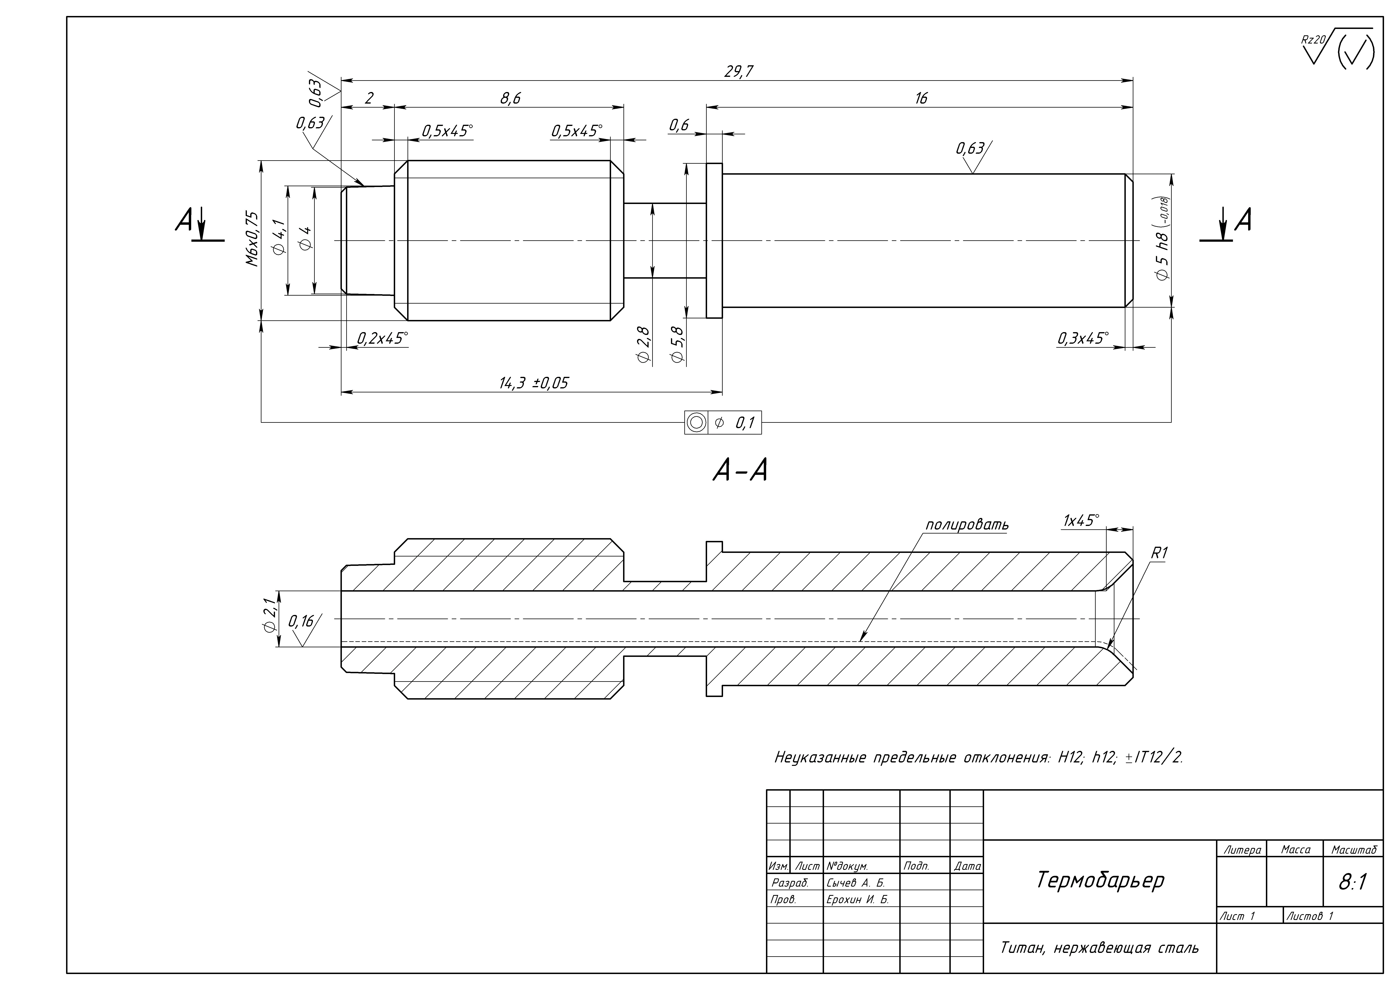
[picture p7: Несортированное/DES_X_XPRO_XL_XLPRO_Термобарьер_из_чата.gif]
DES_X_XPRO_XL_XLPRO_Термобарьер_из_чата


1.  Чертёж_обойма_роликов_624ZZ
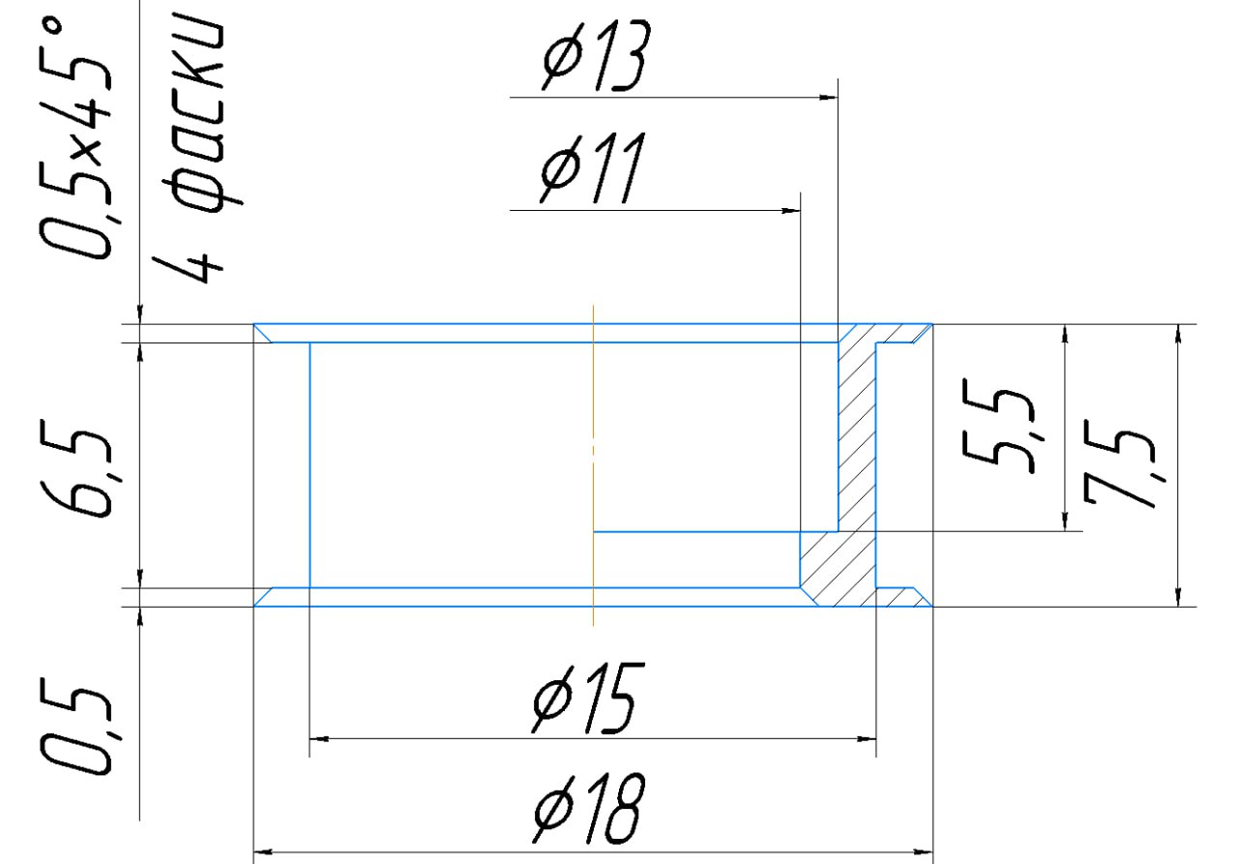
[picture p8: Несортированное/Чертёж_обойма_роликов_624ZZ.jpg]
Чертёж_обойма_роликов_624ZZ


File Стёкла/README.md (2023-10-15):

# Стёкла Designer XPRO, X, XL, XLPRO

Стёкла (цветное, матовое, зеркало — какое больше нравится) возможно нарезать на стеколке по чертежу. Не закалённое стекло. Стекло после закалки не режут. Фаска по желанию, можно просто обработать кромку [^1].

Толщина стекла Designer X, XPRO — 4 мм, Designer XL, XLPRO — 8 мм.

Первое время Picaso поставляли стёкла для XPRO с выемкой 12 мм, затем стали поставлять с выемкой 10 мм. 10 мм в скобу влезает, но с усилием.

> Размеры стекла Designer X S2: 210х215мм. Толщина 4мм. Диаметр выемки 9 или 10мм [^2]. 

Углубления под магниты обычно на стеколке никто не хочет делать. Как вариант, можно купить тонкие магниты (0,5мм) и наклеить без углублений — отметить маркером точки и по ним наклеить.

Стекло без магнитов крепится канцелярскими прищепками или кастомными зажимами.

Возможные варианты клея для магнитов: УФ, поксипол, эпокси-металл. Picaso клеят магниты на Loctite EA 9514.

Возможно заказать матовые стёкла (пескоструй или химия) для получения первого слоя с матовой фактурой.

> PicasoXL_glass_template_v8.stl — шаблон для приклейки магнитов на стекло для XL [^3].

XPRO_Стекло_var.0          |  XPRO_Стекло_var.1
:-------------------------:|:-------------------------:
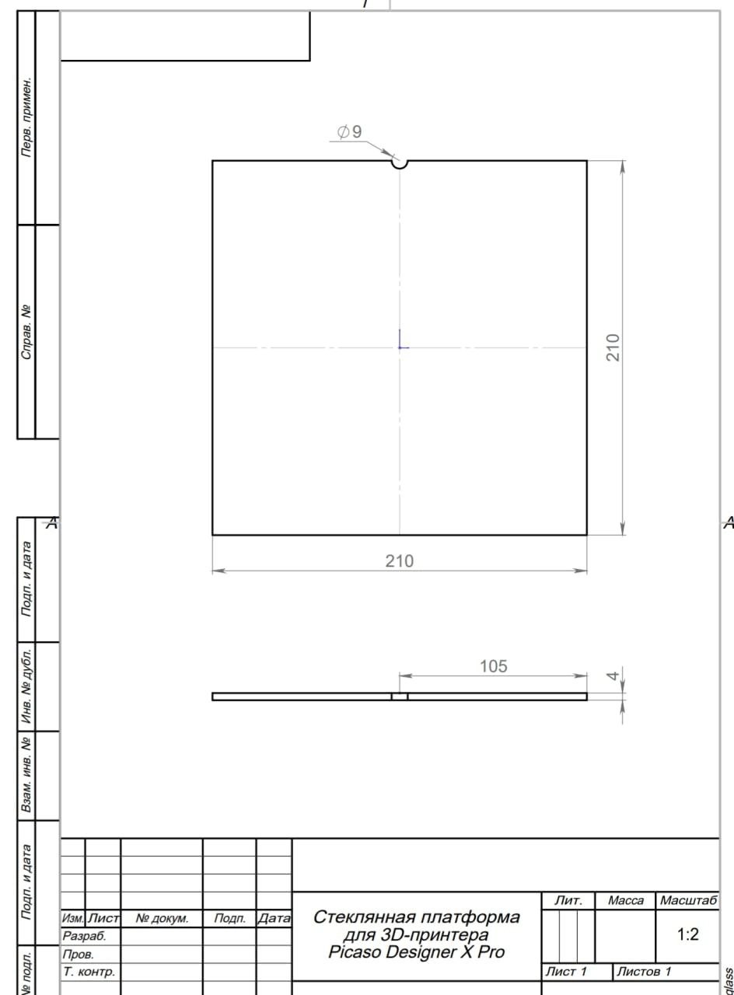
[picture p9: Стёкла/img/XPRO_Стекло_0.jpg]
XPRO_Стекло_0
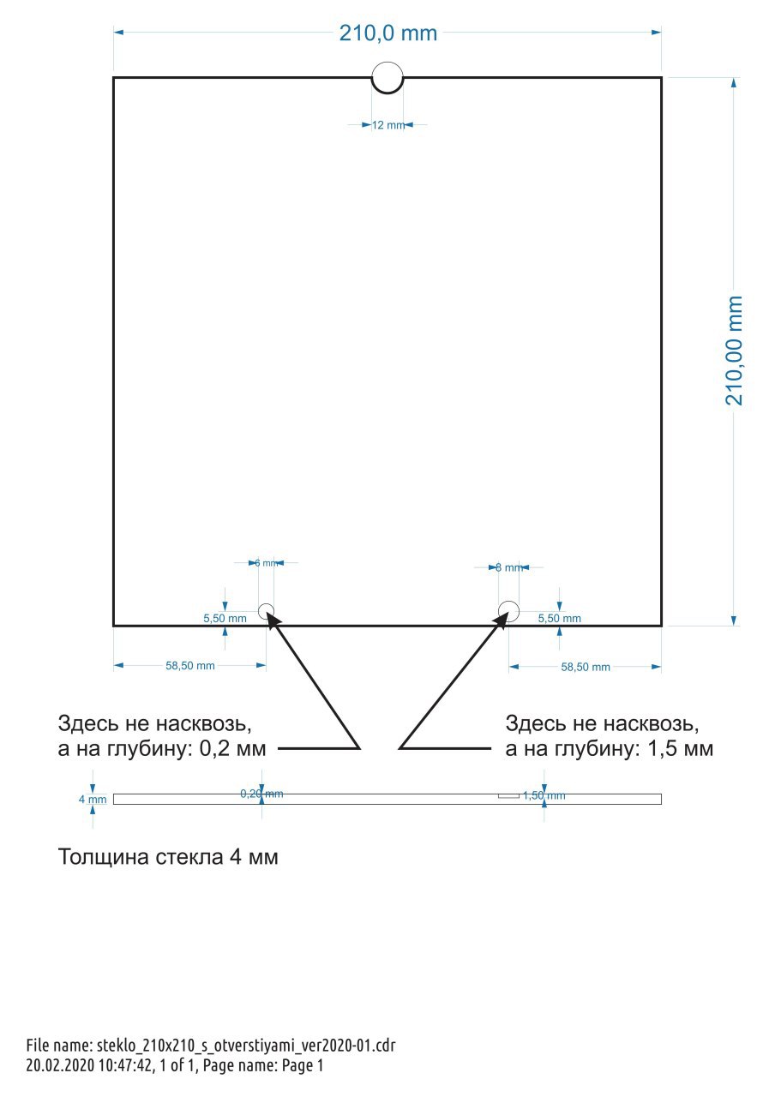
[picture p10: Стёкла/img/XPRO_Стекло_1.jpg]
XPRO_Стекло_1
 | 

250PRO_стекло_var.0        |  250PRO_стекло_var.1
:-------------------------:|:-------------------------:
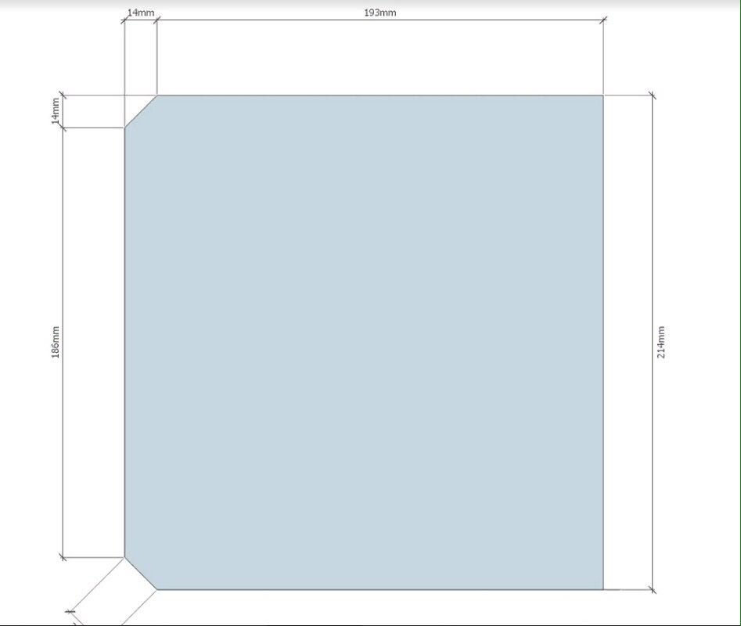
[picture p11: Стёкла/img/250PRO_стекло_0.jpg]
250PRO_стекло_0
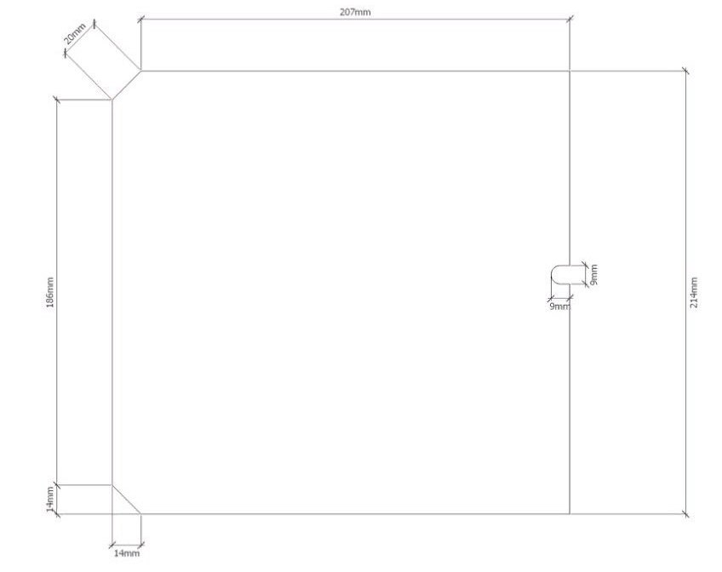
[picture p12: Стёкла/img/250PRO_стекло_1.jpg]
250PRO_стекло_1
 | 

Стекло XL, XL PRO          |
:-------------------------:|
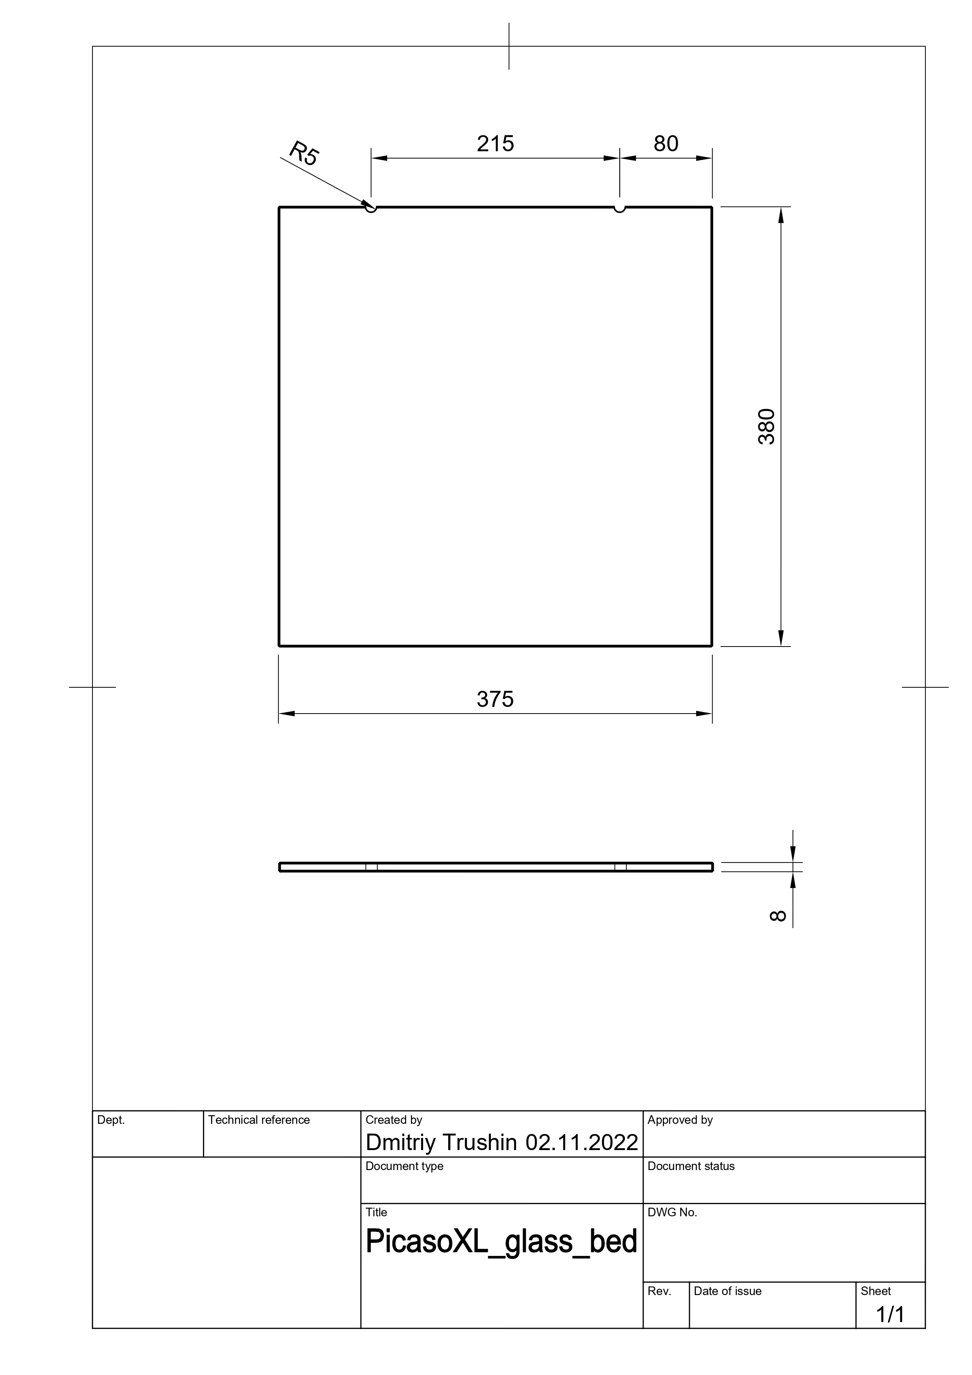
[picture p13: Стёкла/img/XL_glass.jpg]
XL_glass


Матовое стекло (химия):

<p float="left">
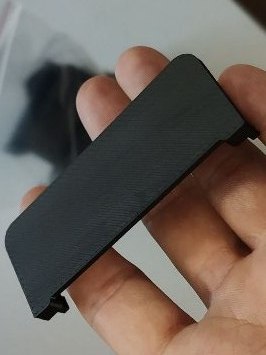
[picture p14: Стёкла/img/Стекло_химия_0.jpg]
Стекло_химия_0
  
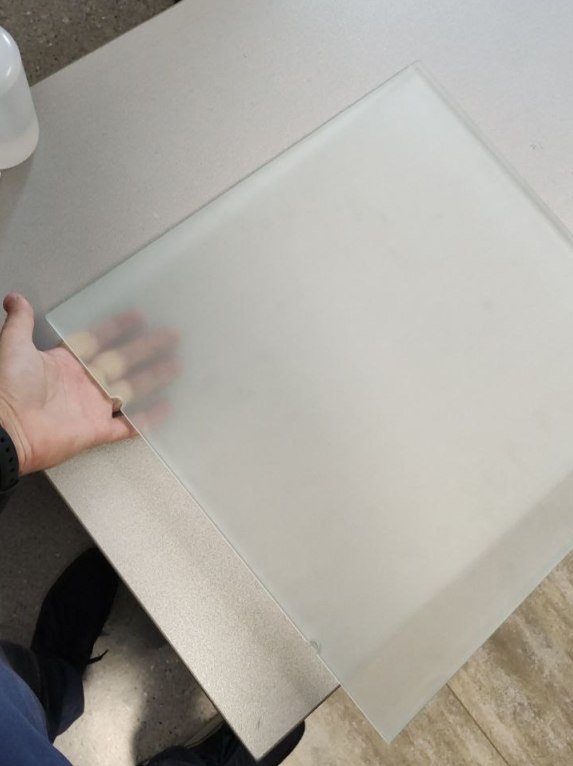
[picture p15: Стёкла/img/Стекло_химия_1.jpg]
Стекло_химия_1
  
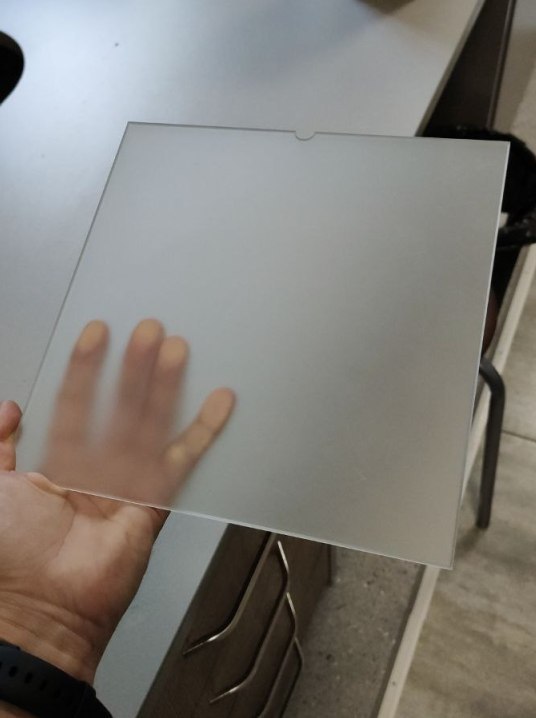
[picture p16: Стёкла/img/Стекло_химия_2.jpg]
Стекло_химия_2
  
</p>

[^1]: Telegram [Источник](https://t.me/Picaso3dUnofficial/253018)
[^2]: Telegram [Источник](https://t.me/Picaso3dUnofficial/278477)
[^3]: Telegram [Источник](https://t.me/Picaso3dUnofficial/268936)

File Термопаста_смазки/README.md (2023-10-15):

1. Термопаста_Gripcott_NF

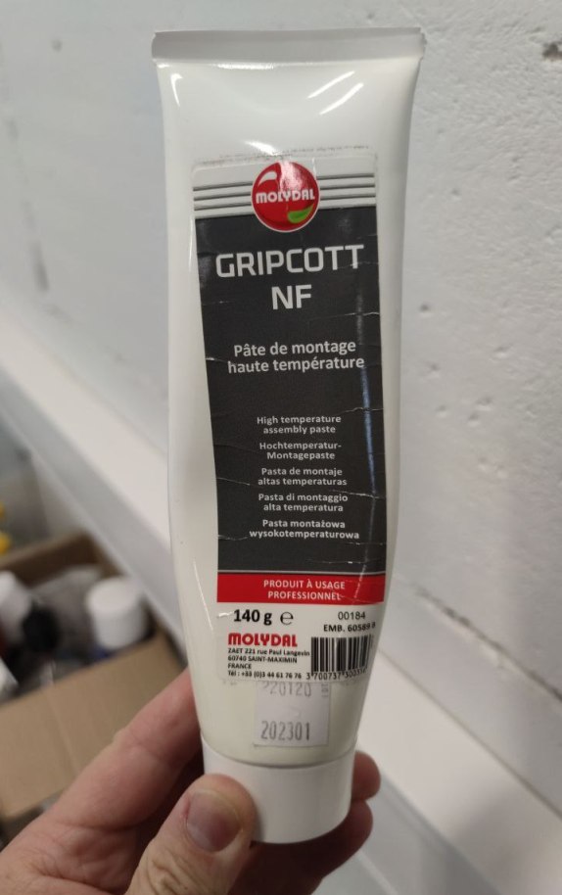
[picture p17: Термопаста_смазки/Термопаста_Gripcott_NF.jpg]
Термопаста_Gripcott_NF


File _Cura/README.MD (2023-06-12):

# Добавление принтера Picaso Designer X, Designer X PRO в Cura

В зависимости от версии Cura, содержимое папки resources из архива Ultimaker **Cura_PicasoX.zip** распаковать в соотвествующую папку (указаны пути установки Cura по-умолчанию):

**Cura 5.x:**
C:\Program Files\Ultimaker Cura 5.x\share\cura\resources\

**Cura 4.x:**
C:\Program Files\Ultimaker Cura 4.10\resources\

1. Запустить Cura. В списке доступных принтеров появится Picaso/Designer XPro.

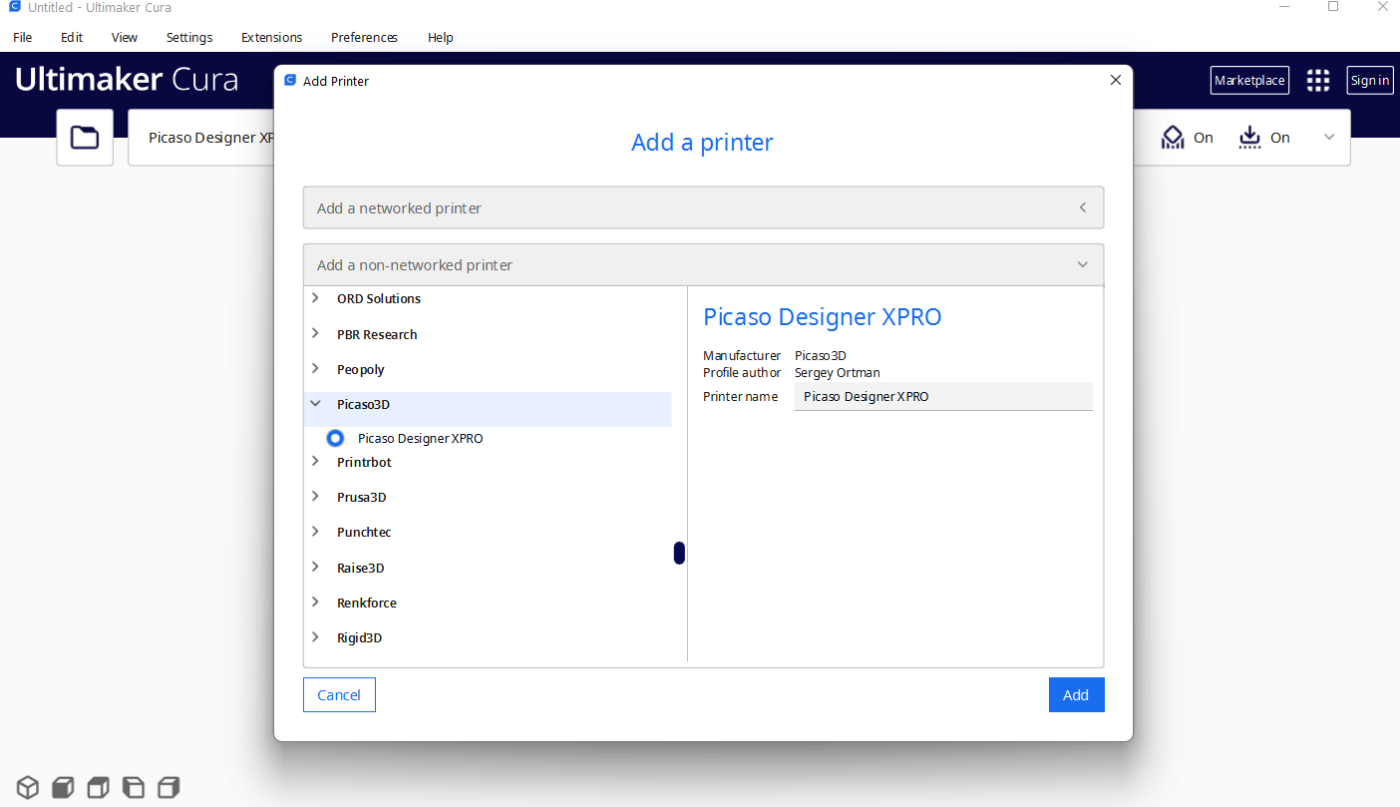
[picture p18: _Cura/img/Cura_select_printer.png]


2. В поле «Начальный G-код для экструдера», чтобы после переключения сопел активное сопло прочищалось в специальном очистителе, необходимо прописать:

*Extruder 1 Start G-code (для первого или единственного экструдера):*

```
T10 I5 S1 R1 P1
```

*Extruder 2 Start G-code (для второго экструдера):*

```
T11 I5 S1 R1 P1
```

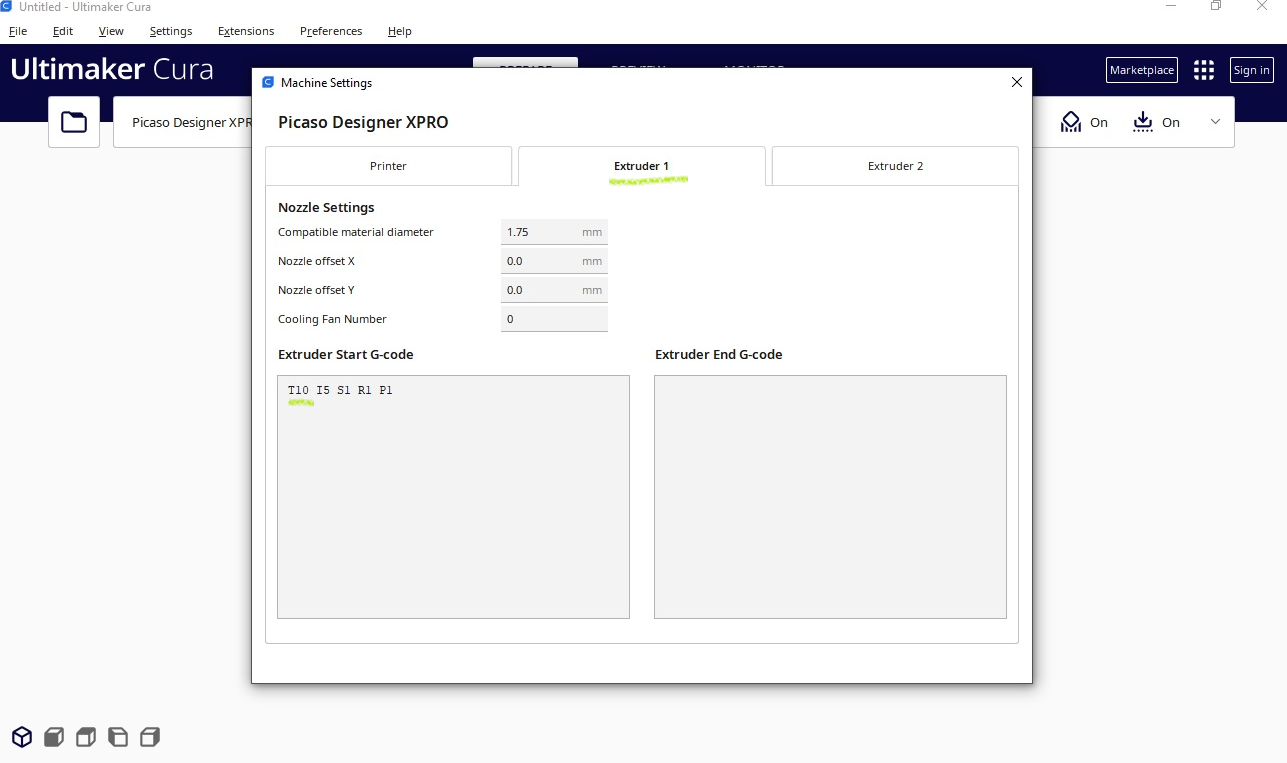
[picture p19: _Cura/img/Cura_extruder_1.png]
cura_extruder_1


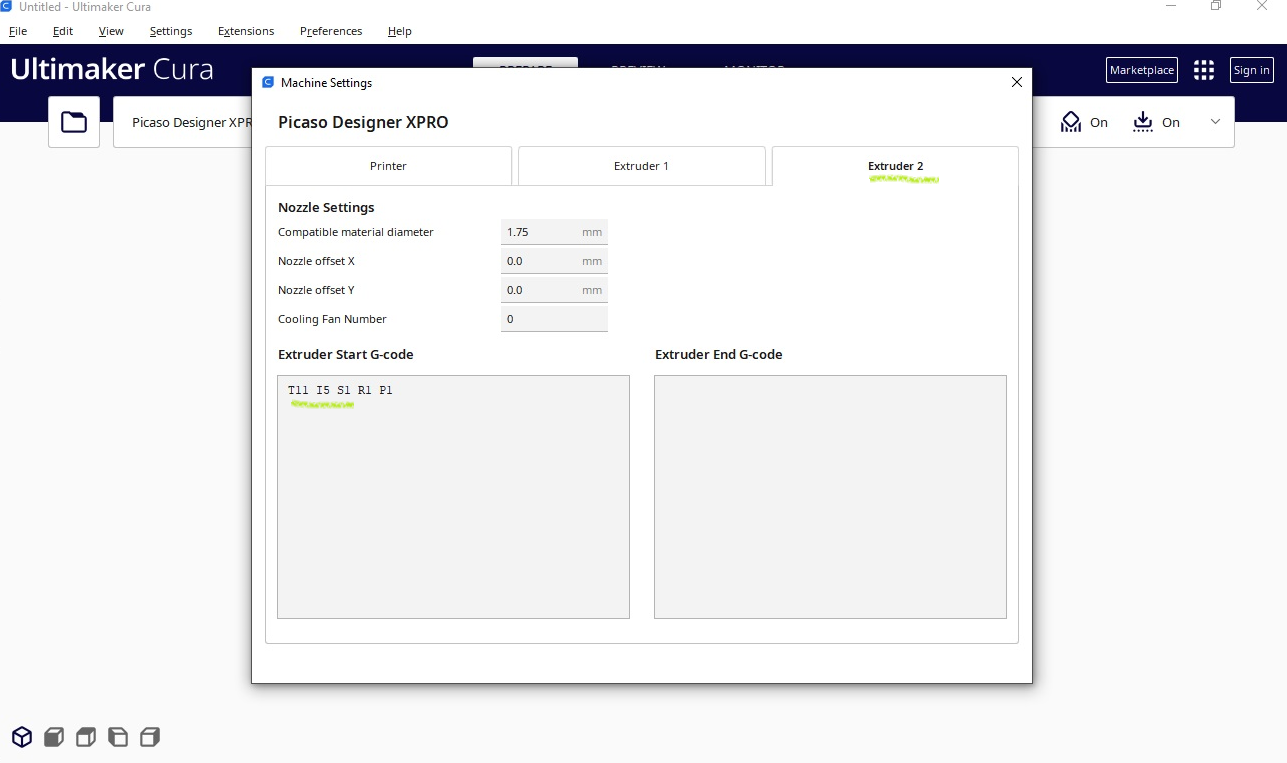
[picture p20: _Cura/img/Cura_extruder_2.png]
cura_extruder_2


>Для очистки сопел возможно использовать черновую башню, а не сопливчики: для этого в настройках принтера включить "быстрое переключение сопел".

Для Designer X необходимо изменить количество экструдеров (extruder count) = 1.

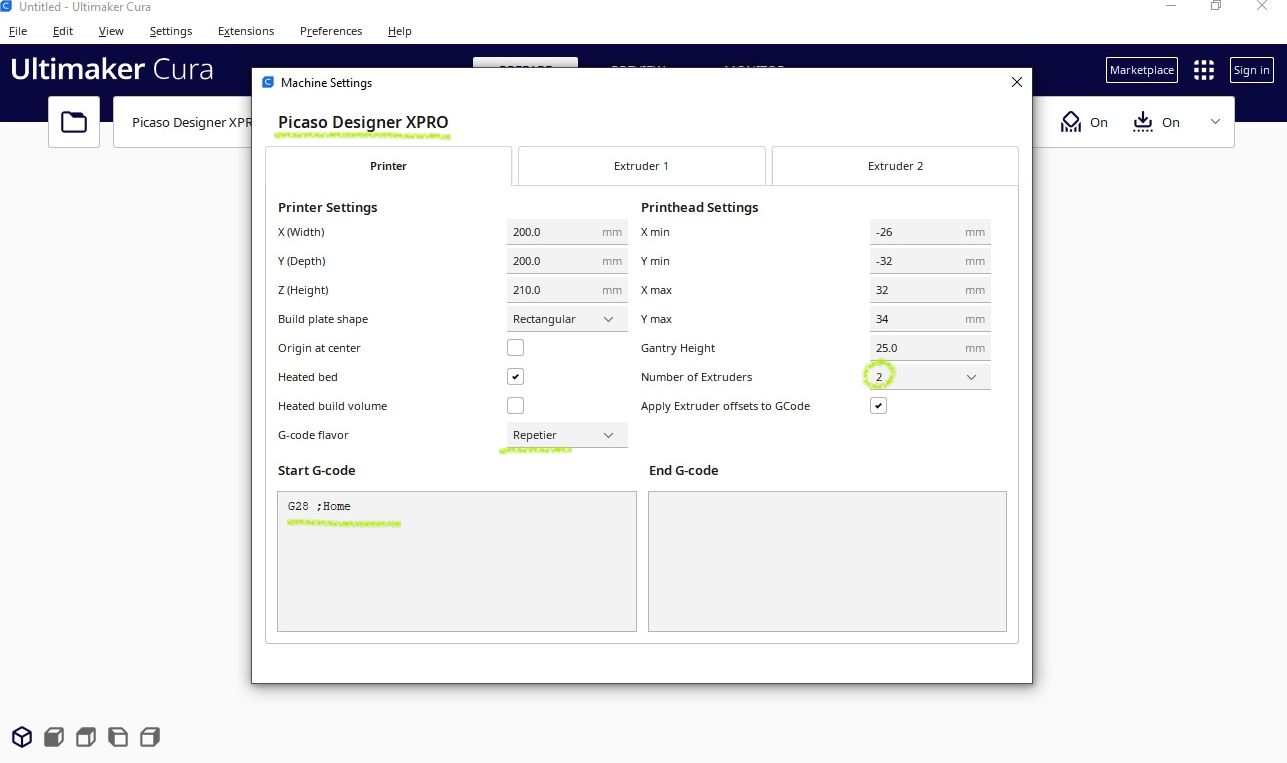
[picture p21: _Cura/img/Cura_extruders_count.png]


>X-серия сама всё умеет делать и при печати G-кода принтер выполняет зашитый в прошивку обязательный код перед печатью и после печати.

3. Для корректной работы системы контроля подачи пластика добавьте специальный скрипт. Для этого в меню *Extensions > Post processing > Modify G-code* нажмите *«Add a script»* и выберите *Search and Replace*. Впишите следующие скрипты:

*Search:*

```
;LAYER:
```

*Replace:*

```
M532 X0 L
```

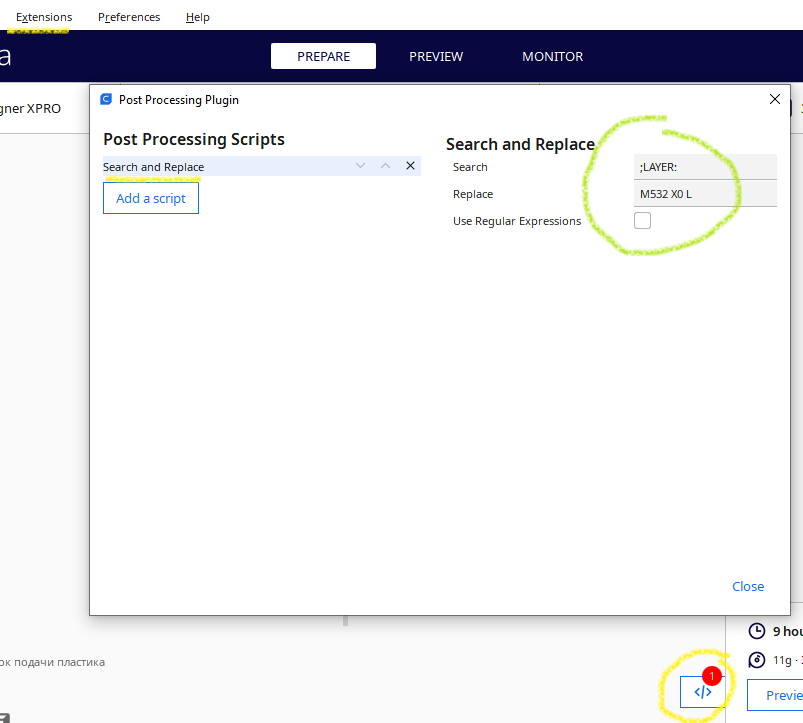
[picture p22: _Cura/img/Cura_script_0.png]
cura_script_0


>Дополнительная информация и инструкция по использованию сторонних слайсеров (Cura, PrusaSlicer) для принтеров Designer Classic, X, XPro, XL, XLPro в [Центре поддержки](http://helpcenter.picaso-3d.ru/we-answer).

---
# Picaso Designer

Пример стартового и завершающего G-кода для Picaso Designer.

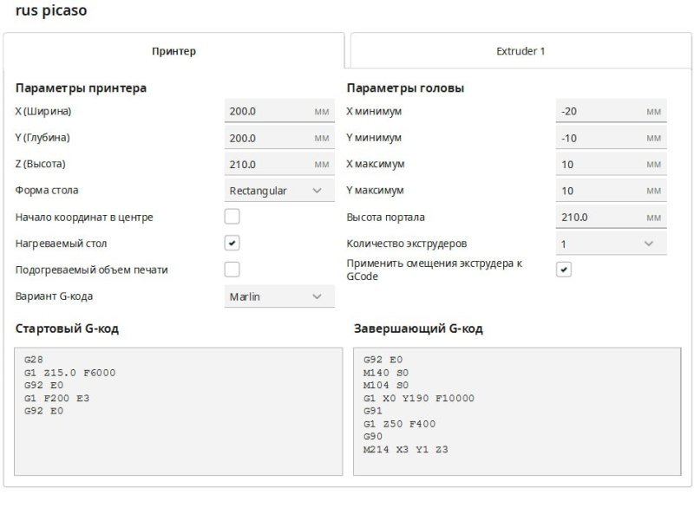
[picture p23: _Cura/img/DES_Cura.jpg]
DES_Cura


Также примеры стартового кода для Picaso Designer и PRO250 есть [в статье про Simplify3D](https://github.com/Octopusmode/Picaso3D/tree/master/_S3D_%D0%B4%D0%BB%D1%8F_Picaso_%D0%A1%D1%82%D0%B0%D1%82%D1%8C%D1%8F_%D0%BE_%D0%BD%D0%B0%D1%81%D1%82%D1%80%D0%BE%D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).

<picture><source media="(prefers-color-scheme: dark)" srcset="https://cdn.simpleicons.org/telegram/white"> <source media="(prefers-color-scheme: light)" srcset="https://cdn.simpleicons.org/telegram/black"> Telegram</picture> [Источник](https://t.me/Picaso3dUnofficial/275116)

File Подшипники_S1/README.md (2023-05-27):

# Подшипники для принтеров X, XPRO, XL, XLPRO серии S1

Слева направо:

1. Китайские MR63 и широкая шайба (толщина 0,8 мм, самая широкая, что получилось найти). Данный вариант был установлен в качестве эксперимента. Итог эксперимента отрицательный. Шайба слишком широкая, упиралась в пластину и клинила;

2. Итальянские MR63 (куплены у Picaso3D) и широкая шайба. Также неудачный вариант из-за широкой шайбы. В итоге широкая шайба была заменена на обычную;

3. Китайские MR63 и обычная шайба (М3, толщина 0,5 мм), как эталонный образец;

MR63: https://aliexpress.ru/item/4000891710951.html

4. Фланцевый подшипник MF63ZZ, без шайбы;

В данном случае на ведомой оси используется комбинация из открытого MR63 и закрытого фланцевого MF63ZZ подшипников (при этом шайба не используется): есть отзывы из эксплуатации, что закрытые подшипники реже клинят. Закрытый фланцевый подшипник ставят на ведомую ось спереди (без шайбы), а сзади — открытый. Два закрытых фланцевых одновременно установить невозможно, так как толщина MR63 — 2 мм, MR63ZZ — 2,5 мм, в итоге два закрытых фланцевых подшипника просто не умещаются (вернее умещаются, но не тогда не нужно до конца закручивать винты крепления). Фланцевый подшипник возможно установить без приклеивания его на вал, так как он плотно зажимается и без клея. 

Также вместо фланцевого закрытого возможно установить просто закрытый подшипник MR63ZZ, без шайбы, он также имеет толщину 2,5 мм, по опыту участников чата его не приклеивают, устанавливается он на ведомую ось спереди и с вала не соскакивает. На момент октября 2022 года MR63ZZ ставится производителем на XL и XLPRO и не приклеиваются на вал.

MF63ZZ: https://aliexpress.ru/item/32880777629.html

MF63ZZ: https://aliexpress.ru/item/32859031010.html

MR63ZZ: https://aliexpress.ru/item/32834097040.html

5. Керамика MR63 с обычной шайбой (М3, толщина 0,5 мм).

Керамика MR63: https://aliexpress.ru/item/4000960298577.html

Вариант (1) сразу оказался неработоспособным из-за толщины шайбы. В итоге в эксперименте участвовали варианты (2), (3), (4), (5). Итальянские с широкой шайбой, которая в итоге была заменена на обычную (2), китайские с обычной шайбой (3), фланцевый подшипник (4) ходят примерно одинаковое количество часов (600-1000 часов в среднем, иногда время работы доходит до 3500-5000 часов). Керамический с обычной шайбой на момент эксперимента оказался самым надёжным, но на момент ноября 2022 года нет статистики использования керамических подшипников и информации каким образом они выходят из строя (возможно, лопается). Чаще всего в качестве кастомного варианта применяют закрытые или фланцевые подшипники.

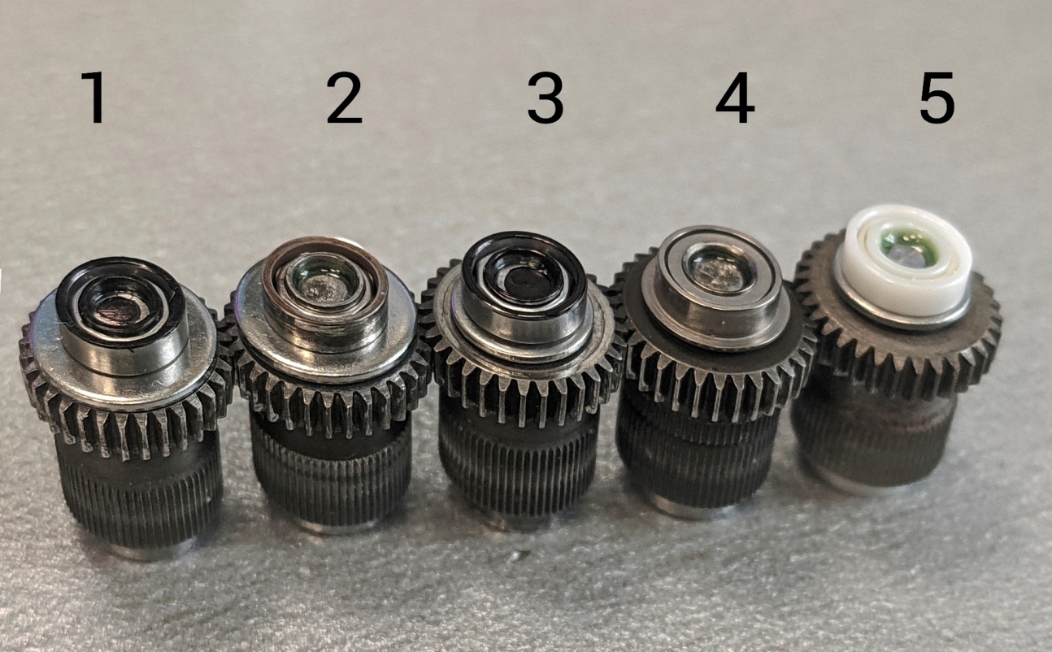
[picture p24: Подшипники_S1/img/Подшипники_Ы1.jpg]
Подшипники_Ы1


6. Подшипники MR63ZZ толщиной 2мм, закрытые.

https://sl.aliexpress.ru/p?key=5mCDtyv

MR63ZZ_2mm

Техподдержка Picaso3D рекомендует приклеивать передний подшипник (в случае использования открытого толщиной 2 мм) к валу с ведущей шестернëй, чтобы он не слетел с вала и шестерня не начала цепляться за радиатор, вырабатывая его:

Центр_поддержки_посадка_подшипников

По опыту участников чата приклеивать подшипник можно на цианакрилатный клей, желательно перед этим обезжирить поверхность. Будьте аккуратны, в случае использования цианакрилатного клея подшипник может очень быстро приклеиться к валу, и не удастся его правильно расположить. Клей должен быть только между внутренней обоймой подшипника и валом.

Также некоторые участники рекомендуют смазывать подшипники перед установкой в принтер для увеличения их срока службы. После набивки подшипников смазкой важно убрать её излишки.

Снять приклеенный подшипник возможно либо механически расколов его, либо путём нагрева паяльным феном с температурой около 500°С и постепенно просовывая в зазор между подшипником и шестернёй лезвие.

Теоретически возможно использовать подшипники MR63 2RS, но на момент ноября 2022 года такой эксперимент в сообществе никто не проводил.

Используемая маркировка подшипников:

+ MR — открытый подшипник (миниатюрный метрический шариковый подшипник);

+ MF — фланцевый (миниатюрный метрический шариковый подшипник с фланцем);

+ RS — один резиновый пыльник (контактное уплотнение из каучука, прорезиненное уплотнение);

+ 2RS — два резиновых пыльника;

+ Z — защитная металлическая шайба с одной стороны;

+ ZZ — защитная металлическая шайба с двух сторон ("закрытый" подшипник).

<picture><source media="(prefers-color-scheme: dark)" srcset="https://cdn.simpleicons.org/telegram/white"> <source media="(prefers-color-scheme: light)" srcset="https://cdn.simpleicons.org/telegram/black"> Telegram</picture> [Источник](https://t.me/Picaso3dUnofficial/244110)

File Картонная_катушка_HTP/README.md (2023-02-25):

# Втулка картонной катушки HTP

Для тех, кому надоели разваливающиеся картонные катушки от HTP.

Диаметр отверстия под держатель 45мм, посадочный диаметр под катушку 80мм.

Садится плотно, и можно обойтись без винтов.

HTP_0

<picture><source media="(prefers-color-scheme: dark)" srcset="https://cdn.simpleicons.org/telegram/white"> <source media="(prefers-color-scheme: light)" srcset="https://cdn.simpleicons.org/telegram/black"> Telegram</picture> [Источник](https://t.me/Picaso3dUnofficial/244468)

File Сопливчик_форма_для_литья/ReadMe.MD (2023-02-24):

# Чистики для принтеров Picaso

По ТТХ прям один в один, та же жесткость, геометрия и температуростойкость. 
Силикон без коллера, поэтому чистики прозрачные.

В файлах есть модель самого чистика, её можно модернизировать при желении.
Два .stl файла с уже заложенным допуском специально для печати, чтобы ответная часть закрывалась.

Силикон на основе платины твердостью 20 по Шору оказался сильно мягким и чистики не выполняли свою функцию.
Для литья лучше использовать силикон на платине с твердостью 40 по Шору.
Формы из PLA.

Силикон можно купить на Ozon'е или, например, по ссылке: https://sintez-mold.ru/product/silikon-dlya-pishhevyh-form-liquidform-platinum-40-1kg/

<p float="left">
  Силикон
  Форма_для_литья_0 
  Форма_для_литья_1
</p>

<picture><source media="(prefers-color-scheme: dark)" srcset="https://cdn.simpleicons.org/telegram/white"> <source media="(prefers-color-scheme: light)" srcset="https://cdn.simpleicons.org/telegram/black"> Telegram</picture> [Источник](https://t.me/Picaso3dUnofficial/239314)

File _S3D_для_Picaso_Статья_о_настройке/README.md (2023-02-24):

# Как настроить слайсер Simplify3D под 3D принтеры Picaso 3D Designer

> Спойлер «Если ищете готовый .FFF профиль, то он в самом низу»

# Предисловие

Задачи, цели и способ их реализации у всех разные, поэтому бессмысленно спорить о том, какой слайсер лучше (если это не новая кура с кучей багов, конечно 🌚).

PolygonX по-своему прекрасен: он даёт возможность не вникать особо в настройки и меньше переживать о забытой галочке в одной из сотни вкладок - все настройки на виду, ничего сверхсложного нет. И вот за это ему огромный респект — лично он мне пару лет назад он помог относительно безболезненно начать работать с аддитивщиной. А с грядущим обновлением движка и расширением возможностей он должен стать ещё лучше.

# Вы точно этого хотите?

Если у вас нет времени ковыряться с настройками (а его понадобится много, чтобы вникнуть во все тонкости), нет задач, которые не решались бы инструментами Polygon и вы хотите просто стабильный хороший результат — продолжайте пользоваться Polygon и не тратьте зря время (серьёзно).

А еще при печати .GCODE (расширения файла, который формирует Simplify3d или Cura) вы теряете поддержку работы пары датчиков, за которые вы уже заплатили денюжку. Как минимум – теряете контроль поверхности и возможность регулировки прижима на первом слое, как максимум – еще и контроль наличия прутка и контроль подачи (защита от проскальзываний). Далее также поясню, откуда все эти минимумы и максимумы.

Разбирать подробно каждую вкладку в не буду, т.к. об этом есть как сотня других статей, так и подробное описание каждой настройки на сайте самого Simplify3d (далее s3d).

# Мотивы

Главной причиной, наверное, по которой мне стало не хватать Polygon'а — настройки поддержек. Ну уж очень сильно прикипали отделяемые поддержки и плохо выходили мосты. Те, кто печатает из Polygon'а должны знать ту боль, что можно испытать при отделении поддержек под 90 градусов, к примеру, из PETG. Причем боль эта может быть не просто моральной, а есть вероятность реально травмироваться. Причиной тому — отсутствие настроек изменения скорости перемещения и интенсивности обдува при печати нависаний над этими самыми поддержками. Иногда эти поддержки просто становились частью корабля детали и ничего с этим уже не сделать без электроинструмента и необоснованной траты уймы времени.

1_picasimp

Но и эти настройки также обещают добавить когда-нибудь в новой версии Polygon 2.0, так что если вы и до сюда дочитали, то подумайте в третий раз.

# Так вот…

Simplify3d — платный слайсер и это ещё один повод передумать.

2_picasimp

150 зелёных придется отвалить за не ограниченную временем лицензию на 2 одновременно использующих слайсер устройства, есть триал версия на 2 недели.

Поддержка обновлений до свежих версий на 1 год звучит смешно, т.к. последнее обновление выходило больше года назад и будет ли вообще — неизвестно (но вроде как обещают всё-таки).

С другой стороны, пиратку никто не отменял — хоть и с некоторыми багами, но работать с ней вроде как можно (на свой страх и риск).

# Много воды, давай уже по делу

Для начала необходимо выбрать, на какой прошивке работает принтер.

## 1. Tools -> Firmware Configuration

3_picasimp

Тут просто выбираем «RepRap (Marlin…)»

И всё, ничего не меняем.

4_picasimp

Давным-давно, на старых прошивках принтеров (около 4.0) были проблемы с запуском обдува из s3d и приходилось настраивать параметры в этом окне, но эти тяжёлые времена прошли и теперь все просто. Я специально заострил внимание на этом, потому что в сети ещё остались статьи, которые не актуальны для свежих прошивок.

Все, просто закройте окно, нажав кнопку «Save» и забудьте о нем.

## 2. Tools -> Options

5_picasimp

Здесь во вкладке «Machine» нам нужно настроить форму области построения, систему координат и объём. Выбираем «Cartesian robot (rectangular build volume)» и длины осей: 200x200x210мм. В общем, всё на скрине:

6_picasimp

Не забываем нажать «ОК».

Эту вкладку настраивать не обязательно, но мы сделали это на всякий случай. Далее объясню, зачем.

## 3. Add

В левом нижнем углу. По этой кнопке создаётся новый процесс. В нем будем настраивать новый профиль для принтера.

7_picasimp

8_picasimp

Мы же профессионалы — сразу же нажимаем «Show Advanced».

## 4.  Add Extruder

Настраивать s3d будем сразу под двухэкструдерную печать на Picaso Designer XPro. Это самый универсальный вариант, т.к. можно будет пользоваться одним профилем для подготовки заданий и для XPro и для X.

Добавляем второй экструдер:

9_picasimp

У меня их зовут LEFT и RIGHT, как ни странно. Это рабочие названия чисто чтобы самому не запутаться. Можете назвать их как душе угодно: Чип и Дейл, Малыш и Карлсон, Пупа и Лупа.

## 5. Tool 0, Tool 1

Так вот, чтобы экструдеры верно определялись в слайсере, нужно обозначить для каждого из них свой инструмент. В Picaso левое сопло — это «Tool 0», а правое — «Tool 1».

10_picasimp

11_picasimp

Соответственно, настройки ширины экструзии и ретрактов настраиваются в этой же вкладке.

## 6. Temperature

Во вкладке «Temperature» также необходимо добавить 3 контроллера температуры: для двух сопел и для стола.

12_picasimp

Каждому из контроллеров нужно присвоить идентификатор.

Для сопел он должен соответствовать номеру инструмента из вкладки «Extruder»: LEFT — *T0*, RIGHT — *T1*, BED — *T0*.

Для сопел ставим галочку «Extruder», для стола «Heated build platform».

13_picasimp

Чуть ниже есть галочка «Wait for temperature controller to stabilize before beginning build» - советую тоже на всех контроллерах включить, чтобы сопло дожидалось прогрева стола и наоборот.

## 7. G-CODE

В этой вкладке мы видим настройки, которые уже, казалось бы, настроили в п.2. Это как раз то, о чём я говорил ранее: настроить принтер можно как в профиле печати, так и установить их общие для всех профилей слайсера(в случае отключенных галочек «Update». Если настройки прошивки принтера или области построения и т.д. отличаются для этого профиля от общих, можно их выставить здесь. Если у вас нет других принтеров, кроме Х и Х Pro, то обе эти галочки ни на что не повлияют, т.к. мы все настроили ранее. Но если есть XL или XL Pro, то для их профилей нужно будет выставлять отдельно другие настройки области построения.

14_picasimp

Остальное — как на скрине, если вдруг что-то отличается.

## 8. Scripts

Тут будет разделение на старые и новые принтеры:

- пункт 8.1 — если у вас первый Designer или PRO250;

- пункт 8.2 — если у вас любой другой Picaso (кроме Builder`а, конечно).

> Starting Script — это код, который будет исполняться непосредственно перед заданием, которые вы заботливо подготовили для принтера.

> Ending Script — код после задания.

> Tool Change Script — код с условием, выполняемый при смене инструмента.

### 8.1. Designer, PRO250

15_picasimp

Scripts -> Starting Script:
```
M85 S600
G21
G90
M82
G28
G90
T10 I5 S1
```

Scripts -> Ending Script:
```
T0
M140 S0
M104 T0 S0
M104 T1 S0

G1 X0 Y190 F10000.0
G91
G1 Z50 F400
G90
M214 X3 Y1 Z3
```

Scripts -> Tool Change Script:
```
{IF NEWTOOL=1}T11 I8 S1 R1;
{IF NEWTOOL=0}T10 I8 S1 R1;
```
И описание по паре пунктов:

> T11 — это команда печатающей головке (ПГ) отправиться к правому чистику (соответственно, *T10* — к левому);

> I8 — выдавить в чистик 8мм пластикв.

По остальным командам — можно погуглить, т.к. они стандартные.

### 8.2. Picaso Designer X, XPro (для XL и XLPro тоже должно работать, но ко мне XL приедет только через неделю – проверю)

15_picasimp

Scripts -> Starting Script:
```
G28
```
Scripts -> Ending Script:

ПУСТО (нет, не надо писать «пусто» — просто оставьте эту вкладку пустой)

Scripts -> Tool Change Script:
```
{IF NEWTOOL=1}T11 I8 S1 R1;
{IF NEWTOOL=0}T10 I8 S1 R1;
```
Да, в стартовом коде всё по-простому, без изыска, а конечный код вообще пустой — Икс-серия сама всё умеет делать и принтер выполняет какой-то обязательный код перед печатью и после печати.

А тулченж такой же, если хотите использовать чистики при смене сопла.

Если у вас односопельный принтер, то просто выбираете во всех вкладках печать соплом с идентификатором *T0* (у меня это LEFT).

## 9. Настройки двухэкструдерной печати

### 9.1. Layer

Выбираем главный инструмент (в моём случае — левое сопло с инструментом *T0*), который будет использоваться для печати внутренних и внешних периметров модели. Тут же выбирается высота слоя (чуть ниже) и т.д.

16_picasimp

### 9.2. Additions

Выбираем инструмент для печати юбки или брима. Если нужно усиление контакта, то выбираем левое сопло. Если вокруг модели поддержка — правое, чтобы контакт лучше был у нее, ну и так далее — поковыряйтесь сами.

17_picasimp

В этой вкладке есть ещё пара полезных функций для двухсопельной печати. Это Prime Pillar и Ooze Shield.

Первую рекомендую к использованию всегда, т.к. часто от чистика до модели далековато и мокрые или плохо настроенные филаменты подтекают, а также для сбора лишнего давления. Есть вариант использовния башни без чистиков совсем (для этого просто очищаете вкладку Tool Change Script) — печать будет быстрее, но если плохо настроить, то намного грязнее — всё на свое усмотрение.

Ooze Shield — это некий щит вокруг модели. Для филамента с высокой усадкой использовать для более равномерного остывания крупных деталей, либо альтернативный вариант использования – как дополнительной объект для сброса лишнего давления в сопле.

### 9.3. Infill

Выбираем, каким соплом печатать заполнение. Можно, конечно, печатать его каким-нибудь более дешёвым пластиком, в связке, к примеру ForMAX+ABS, но я ни разу не пользовался, т.к. любая двухсопельная печать — это долго, а время — это амортизация, а амортизация — это деньги, а раз так, то какой смысл от такой экономии?

Ставим основное сопло.

18_picasimp

### 9.4. Support

Самое интересное.

Для односопельной печати просто везде основное сопло выставляем.

Для двухсопельной печати 2 адекватных варианта:

- основа поддержки основным материалом, интерфейсные слои поддержки – материалом поддержки;

- вся поддержка полностью из материала поддержки.

Опыт показывает, что второй вариант надёжнее, т.к. обычно материал поддержки плохо липнет к основном, чтобы легко их разделять. А добавление ещё одного контактного слоя — дополнительный риск. В общем, шанс факапа увеличиваются.

19_picasimp

### 9.5. Temperature

Тут ничего нового, просто следите за настройками в этой вкладке — чтобы тип и идентификатор соответствовали фактическому.

20_picasimp

## 10. Сохраняем профиль

21_picasimp

## 11. Наслаждаемся результатом

Prepare to Print (левый нижний угол).

Выбираем тип отображения линий «Active Toolhead», чтобы удостовериться что нужные элементы печатаются нужным соплом.

23_picasimp

---

Ну и результаты двухсопельной печати на Picaso Designer XPro:

- TPU + PLA(поддержки)

К сожалению, фото с поддержками не осталось, т.к. кто-то добрался до ночного принта раньше меня…

24_picasimp

- PLA+PLA (двухцветная печать)

25_picasimp

- PLA+PVA (eSUN)

Основа поддержки из PLA, интерфейсы — PVA.

Грязновато… Сушите, господа, PVA — не ленитесь.

26_picasimp

- PLA+PVA (REC)

27_picasimp

---

Ну и напоследок — готовый [профиль для Picaso XPro](https://yadi.sk/d/LkV2-d4GFLVlLg).

Стоит отметить, то универсального профиля под любую задачу нет и под конкретную делать и пластик скорее всего не подойдет – придётся поковыряться (основа настроена, конечно же).

Для импорта: File -> Import FFF Profile

## И напоследок, о датчиках

Наладить работу датчиков наличия прутка и контроля подачи можно, вставив некоторый код в некоторое место:

```
{REPLACE "; layer " "M532 X0 L"}
{REPLACE ", Z = " " Z"}
```

28_picasimp

Поясню, что сам я не пользуюсь этими датчиками, но уважаемые люди из телеграм-чата [Picaso3dUnofficial](https://t.me/Picaso3dUnofficial) по принтерам Пикасо вполне себе пользуются. Буду срочные вопросы — лучше сразу там спросить.

Всё это искусство мы успешно практикуем и используем у себя в студии 3D печати [Asteri 3D](https://asteri-3d.ru/) — по смежным вопросам можете обращаться также и туда.

Статья и так получилась намного длиннее, чем планировал, так что не смею больше задерживать.

Удачных принтов и сухого пластика.

05.11.2020

[Источник](https://picaso3d-club.ru/forum/forum44/116-kak-nastroit-slayser-simplify3d-pod-3d-printery-picaso-3d-designer.-statya-dlya-tekh_-kto-khochet-ikh-podruzhit.422)

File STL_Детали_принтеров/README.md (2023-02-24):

# Файлы печатных деталей принтеров

Файлы печатных деталей принтеров, накопленные за время существования телеграмм-группы Picaso3D Unofficial.

Также Хэлпцентр Picaso с stl-файлами деталей принтеров:

[DESIGNER CLASSIC](https://helpcenter.picaso-3d.ru/designer-classic/downloads#!/tab/445779535-3)

[DESIGNER X](https://helpcenter.picaso-3d.ru/designer-x/downloads#!/tab/445594317-3)

[DESIGNER XPRO](https://helpcenter.picaso-3d.ru/designer-xpro/downloads#!/tab/445489983-3)

[DESIGNER XL](https://helpcenter.picaso-3d.ru/designer-xl/downloads#!/tab/445784747-3)

[DESIGNER XL PRO](https://helpcenter.picaso-3d.ru/designer-xlpro/downloads#!/tab/445798095-3)


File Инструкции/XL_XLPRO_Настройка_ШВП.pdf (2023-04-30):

ОБСЛУЖИВАНИЕ И СЕРВИСНЫЕ ОПЕРАЦИИ DESIGNER XL PRO
НАСТРОЙКА ШВП

Инструменты: Шестигранный ключ 1,5 мм (в комплекте), шестигранный ключ 2 мм (в комплекте).

В Designer XL PRO предусмотрена функция автоматической настройки ровности платформы для печати (автоуровень). В настройке участвуют четыре ШВП , регулирующие нужную высоту

1
каждого из углов платформы.


Проведение настройки ШВП может потребоваться, если по завершении настройки стола на экране принтера появляется уведомление “Разброс выше нормы”. Это означает, что после проведения настройки один из углов платформы смещается вниз, создавая слишком большой разброс с замерами других точек.

Убедитесь, что стекло надежно зафиксировано на платформе – оба дальних паза стекла находятся под зажимами, центральный большой магнит установлен в отверстие, нет воздушной прослойки и посторонних предметов между стеклом и платформой.

Для проведения настройки следуйте пошаговой инструкции:

1. Выберите в меню принтера “Сервис > Настройка стола”. Запишите или сфотографируйте цифры на экране принтера во время настройки.

1 ШВП - Шарико-винтовая передача.


i

Числа на экране показывают расстояние (в шагах двигателя) от сопла до соответствующей точки платформы.
Первое значение - показания замера в левом ближнем углу.
Второе - в левом дальнем.
Третье - в правом дальнем.
Четвертое - в правом ближнем.
2. Найдите большее из четырех значений. Таким образом определяется ШВП, которую необходимо настроить.
3. Переведите стол в нижнее положение из меню принтера “Сервис > Положение стола > Нижнее”. Снимите боковые дверцы держателей филамента и катушку пластика с держателя. Извлекать пластик из ПГ при этом необязательно.
4. Выключите принтер.
5. При помощи Г-образного ключа 1,5 подтяните винт на 45° (⅛ оборота) по часовой стрелке.


!
Не перетяните винт, прилагая чрезмерное усилие. Будьте аккуратны! Если винт уже был туго затянут - переходите к шагу 6 инструкции.

i

На гайке ШВП в левом дальнем углу установлен пластиковый ограничитель, защищающий провода. При необходимости регулировки этой ШВП установите ключ через специальное отверстие ограничителя или открутите его при помощи Г-образного ключа 2, если в установленной версии ограничителя отсутствует отверстие для винта.


6. При помощи Г-образного ключа 1,5 подтяните винт с обратной стороны гайки на 45° (⅛ оборота). Визуального доступа к заднему винту нет. При установке Г-образного ключа ориентируйтесь по расположению переднего винта.


7. Включите принтер.
8. Выберите в меню принтера “Сервис > Настройка стола”. Проверьте результат настройки.
i
Если регулируемые винты легко поддавались затяжке, ⅛ оборота может быть недостаточно. В этом случае повторите шаги — с 3 по 8.

Если возникли трудности или вопросы, напишите нам по почте support@picaso-3d.ru

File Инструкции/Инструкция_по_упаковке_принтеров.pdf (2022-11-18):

## Инструкция по упаковке принтеров PICASO 3D для транспортировки

(на примере Designer X PRO)

Инструменты: 5 соединительных стяжек, транспортировочная деталь или 2 фиксатора.

Перед упаковкой принтера извлеките пластиковый пруток из экструдера через меню «Пластик > Извлечь пластик». Если пластик не извлекается, отрежьте пруток на уровне отверстия экструдера. Если ранее были установлены контейнеры, снимите их через функцию меню «Сервис > Снять/поставить контейнеры».
i
Не оставляйте внутри принтера посторонние предметы: пластик, модели, инструменты и пр.

Для упаковки принтера следуйте пошаговой инструкции:
1. Выключите принтер и отсоедините кабель питания.

### 2. Установите транспортировочную деталь с фиксирующими винтами на

заднюю часть стола, либо распечатанные фиксаторы на валы*. Если отсутствует возможность печати, установите отрезок ложемента или пенопласта между дальней частью платформы и планкой, фиксирующей валы.


Установка транспортировочной детали | Установка фиксаторов на валы

* – Скачать модель фиксаторов: https://goo.gl/5Whr6r

### 3. Вращайте центральный винтовой вал (ШВП) против часовой стрелки до

тех пор, пока платформа не займёт крайнее верхнее положение. Если используете транспортировочную деталь, закрутите винты.


4. Зафиксируйте платформу двумя стяжками.

Фиксация стола

### 5. Зафиксируйте печатающую головку в дальнем левом углу при помощи

одной стяжки.

Фиксация печатающей головки

6. Зафиксируйте стекло на платформе двумя стяжками.

Фиксация стекла на платформе

Принтер готов к транспортировке. Сравните с нашим примером:


Пример правильной упаковки принтера
i
При грузовой перевозке, поместите принтер в заводскую коробку с ложементом. При передаче оборудования транспортным компаниям, укажите необходимость упаковки в палетный борт.

При передаче в сервисный центр сохраните у себя оригиналы документов на принтер, USB накопители, кабель питания, контейнеры, пластики и набор инструментов. Отправлять с принтером их не нужно.

Если возникли трудности или вопросы, обращайтесь в техническую поддержку по почте: support@picaso-3d.ru

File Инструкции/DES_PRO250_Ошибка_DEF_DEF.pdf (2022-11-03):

Сообщение DEF DEF.
Сообщение DEF DEF возникает при отсутствии сигнала от датчика (или датчиков) температуры экструдера к контроллеру материнской платы.
Чаще всего, причиной сообщения DEF DEF могут являться:
1) Неисправность датчик температуры


Проверку работоспособности датчика температуры мы начинаем с визуального контроля целостности провода (смотрим, не поломан ли провод) и пропайки соединения «провод-обжимка».
Если провод отломан или порван, его необходимо менять на новый.
Извлекаем белые провода из разъема и визуально проверяем, пропаяны ли данные соединения.


Если пайка отсутствует, необходимо пропаять соединения. Важно, чтобы припой не затек глубоко в разъем, так как это может стать причиной того, что разъем не удастся установить обратно.
После того, как мы убедились, что соединения пропаяны, устанавливаем их в разъем и замеряем сопротивление на датчике температуры. При комнатной температуре окружающей среды сопротивление датчика будет около 1кОм.


Если данные не поступают или сильно отличаются от указанных, то, скорее всего, датчик неисправен и его необходимо менять на новый.

2) Неисправность платы печатающей головки

Чаще всего указанная неисправность выражается в выгорании дорожек на печатаной плате. Необходимо визуально осмотреть плату и убедиться, что выгоревших дорожек нет. Если они присутствуют, то плату необходимо менять.

Если и датчик и плата печатающей головки исправны, но ошибка сохраняется, рекомендуем направить принтер в Сервисный Центр для диагностики.

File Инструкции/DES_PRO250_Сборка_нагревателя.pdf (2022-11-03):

Для сборки нагревателя нам потребуется:
1) Отвертка H1.5
2) Пассатижи
3) Лезвие
4) Шаблон для установки сопла (толщина – 0,5мм, диаметр отверстия – 6,5мм)
5) Термопаста КПТ-8
6) Стопорная жидкость
7) 3-4 шт. стопорных винта 3х4
8) Ключ для замены сопел
9) Термоизолятор сопла (трубка)
10) Латунный блок нагревателя
11) Пара датчик температуры (белые провода)/нагревательный элемент(красные провода)
12) Сопло
13) Корпус блока нагревателя
14) Термоизолятор (керамическая бумага)


1. Возьмем сопло и шаблон для установки сопел. Установим сопло в шаблон и закрутим сопло в латунный блок нагревателя.


Обратите внимание на место установки сопла. Сопло устанавливается со стороны меньшего сквозного отверстия в блоке нагревателя.

2. Проведем протяжку (докрутим сопло до упора) при помощи ключа для смены сопел. Удерживаем латунный блок рукой, другой рукой докручиваем сопло до упора.


3. Нанесем термопасту на термоизолятор сопла.
4. Установим термоизолятор сопла в блок нагревателя. И проведем протяжку термоизолятора. Протяжку осуществляем при помощи ключа для смены сопел и пассатижей. Ключом для смены сопла удерживаем сопло, пассатижами удерживаем термоизолятор и докручиваем его до упора.

Очень важно не погнуть термоизолятор во время выполнения данной операции, поэтому прикладывать излишние усилия или удерживать термоизолятор за край не рекомендуется.


5. Зафиксируем термоизолятор при помощи стопорных винтов и стопорной жидкости. Термоизолятор фиксируется винтами с двух сторон. На кончик винта наносится капелька стопорной жидкости. Винт вкручивается до упора, отвертка должна располагаться по линии винта, отвертка вдавливается в винт, чтобы избежать срыва головки винта. После установки винтов выкручиваем сопло.
6. Выбираем необходимое положение установки пары датчик температуры/нагреватель.
a. Для Designer b. Для PRO 250 (обратите внимание на положение пары)
Левый нагреватель | Правый нагреватель


7. Устанавливаем пару датчик температуры/нагреватель. Наносим термопасту на нагреватель и датчик. Устанавливаем датчик и нагреватель в отверстия. Датчик необходимо устанавливать с приложением дополнительного усилия. Для этого упираем одну сторону нагревателя в ровную поверхность, устанавливаем пассатижи в торец датчика, надавливаем на пассатижи, тем самым устанавливаем датчик в корпус нагревателя.


8. Фиксируем датчик температуры в корпусе нагревателя при помощи стопорного винта. Докручиваем винт до упора.


9. Устанавливаем сопло, керамическую бумагу и корпус блока нагревателя.
Керамическую бумагу устанавливаем таким образом, чтобы ею можно было обернуть нагреватель. Провода необходимо пропустить таким образом, чтобы они не пережимались корпусом блока нагревателя. По мере оборачивания латунного блока нагревателя керамической бумагой загибаем стенки корпуса блока нагревателя. Для того, чтобы закрыть боковые части блока нагревателя необходимо нарезать керамическую бумагу в размер открытых частей.


Перед установкой блока нагревателя в печатающую головку необходимо нанести термопасту на торчащую часть термоизолятора.

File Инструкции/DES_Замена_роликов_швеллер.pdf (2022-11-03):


1. Снять верхнюю крышку с принтера
2. Снять кожух с узла привода печатающей головки

Наша отправная точка для замены роликов.

3. Снимаем боковые стенки узла привода печатающей головки.


4. Извлекаем валы из креплений, расположенных у задней стенки принтера. Для этого вращаем вал и одновременно тянем его вдоль оси на себя. Наша задача освободить швеллер, в котором располагаются ролики.
5. Выкручиваем метизы, удерживающие заднюю стенку узла привода печатающей головки, и убираем стенку.


6. Выкручиваем метизы, удерживающие крепления вала. Они располагаются под креплениями.
7. Извлекаем приводной ремень XY.
8. Извлекаем швеллер с роликами.
9. Схема сборки роликов (левого и правого) представлена на рисунке ниже.


10. Схема установки роликов. Обратите внимание, что сборка роликов имеет различное позиционирование при установке.
11. Сборка роликов завершена.

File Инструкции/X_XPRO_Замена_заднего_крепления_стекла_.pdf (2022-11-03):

XPRO

ИНСТРУКЦИЯ ПО ЗАМЕНЕ ЗАДНЕГО КРЕПЛЕНИЯ ПЛАТФОРМЫ.

Для удобства проведения замены, необходимо подготовить принтер:
- Снять контейнеры для сбора пластика, выбрав в меню принтера “Сервис -> Снять контейнеры”.
- Снять стеклянную платформу.
- Снять боковые стенки принтера с держателями катушек.


Далее приступаем к работе:

### 1. Откручиваем и снимаем боковые фиксаторы стола. Для этого необходимо

выкрутить винт сбоку у каждого фиксатора (рис. 1).


рис. 1

рис. 2


2. Далее, откручиваем центральный фиксирующий винт (рис.2) и 2 винта, удерживающие переднюю планку стола (рис. 2). Снимаем переднюю планку движением вверх.
3. Для извлечения открученного центрального винта, выкручиваем винты, фиксирующие пластиковую деталь (рис.3).

Примечание: При снятии центрального винта, не потеряйте шайбы на его конце. Последовательность установки шайб на рис. 4.

рис. 3

рис. 4


4. После, аккуратно снимаем платформу движением вверх и кладем как на рис. 5.

рис. 5


5. Далее, выкручиваем только средний винт с крестовым шлицем (рис. 6), аккуратно придерживая с задней стороны платформы крепление с T-holder’ом.

рис. 6

После выкручивания и снятия, у Вас должны остаться следующие детали:
- металлическое крепления
- текстолитовая шайба
- T-holder
- металлическая шайба 2шт.

### 6. После замены сломанного крепления, данные детали необходимо установить

строго в определенном порядке, показанном на рис. 7.


рис. 7

Примечание: Обратите внимание, что стальные шайбы необходимо установить гладкой поверхностью вниз (стороной к T-Holder’у).

### 7. После установки, сборка производится в обратной последовательности:

- установить центральный винт, фиксируя пластиковую деталь двумя винтами к стальному каркасу. При закручивании центрального винта, необходимо сверху нажать на заднюю часть платформы, чтобы конец винта попал в T-Holder.
- установить боковые фиксаторы.
- установить переднюю планку стола.

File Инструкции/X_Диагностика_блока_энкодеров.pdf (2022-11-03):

ОБСЛУЖИВАНИЕ И СЕРВИСНЫЕ ОПЕРАЦИИ DESIGNER X
ДИАГНОСТИКА БЛОКА ЭНКОДЕРА

Инструменты: Отвёртка Torx TX-TR (в комплекте), отвертка крестовая.

Принтер Designer X оснащен системами контроля, которые регистрируют наличие и подачу пластика за счет встроенных датчиков. Контроль за филаментом происходит в блоке энкодера.

Диагностика блока энкодера может потребоваться при нестабильной работе встроенных систем контроля.

Для проведения диагностики извлеките блок энкодера (https://docs.google.com/document/d/1lMB-nxN5KlG2TctB5KgpWyJC4zvHuldnjDE76NCrr_Y/edit) из печатающей головки. Замена или ремонт блока энкодера может потребоваться, если:

- установлена версия ролика с резиновым покрытием;
- диск энкодера не вращается или вращается туго;
- имеется люфт оси диска в рычаге;
- имеются заедания рычага в блоке энкодера;
- неверное положение пружины энкодера;
- загрязнены оптические датчики на плате энкодера.
1. Установлена версия ролика с резиновым покрытием.

Убедитесь, что верхнее покрытие ролика с алмазным напылением — это актуальная версия ролика. Если в блоке установлен ролик с резиновым покрытием — замените блок на актуальную версию. Для получения нового блока энкодера — обратитесь в техническую поддержку.


Ролик с алмазным напылением | Ролик с резиновым покрытием

2. Диск энкодера не вращается или туго вращается.

Для проверки вращения раскрутите диск энкодера пальцем. Если диск не вращается или вращается с заеданиями - замените рычаг энкодера или блок энкодера в сборе.
i

Обратите внимание на отклонения диска при вращении. Небольшие отклонения диска допускаются, но при серьезных колебаниях диск энкодера может заедать, задевая корпус блока.


3. Имеется люфт оси диска в рычаге.

Проверьте отсутствие люфта оси вращения диска энкодера в рычаге. Если у оси имеется люфт -аккуратно проклейте место соединения оси с отверстием в рычаге или замените рычаг энкодера / блок энкодера в сборе.
i
В качестве клеящего средства рекомендуется использовать Cosmofen CA-12.


4. Имеются заедания рычага в блоке энкодера.

Проверьте ход рычага в блоке. Если рычаг заедает, задевая корпус блока энкодера — аккуратно устраните причину заедания при помощи напильника или замените блок энкодера.

5. Неверное положение пружины энкодера.

Пружина энкодера в блоке выполняет функцию прижима рычага с диском энкодера к оптическому датчику на плате. Если рычаг с диском недостаточно прижат к датчику, системы контроля могут работать некорректно.
Проверьте состояние пружины. При необходимости, аккуратно отогните пружину или замените блок энкодеров в сборе.

!
Угол отклонения пружины составляет ~30°. Не отгибайте пружину слишком сильно. Это также может привести к некорректной работе системы контроля наличия пластика. Будьте аккуратны!


6. Загрязнены оптические датчики на плате энкодера.

Незаметные загрязнения могут быть причиной некорректной работы систем контроля подачи и наличия пластика. Перед обратной сборкой очистите оптические датчики при помощи любой щетки с жесткой щетиной и спирта.


!
При обратной установке платы энкодера не затягивайте винты слишком сильно. Это может привести к некорректной работе систем контроля подачи или наличия пластика.

По результату проведения диагностики, а также если возникли трудности или вопросы, напишите нам по почте support@picaso-3d.ru

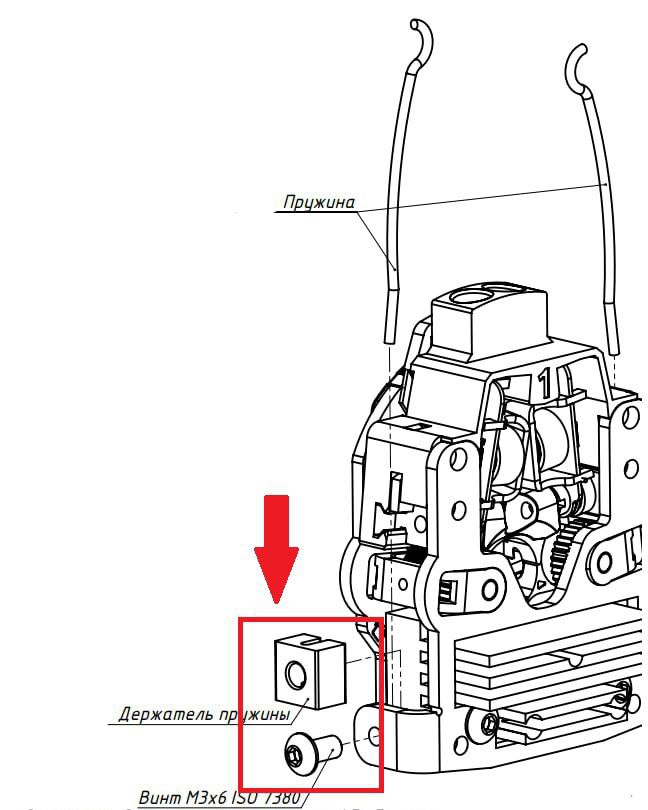
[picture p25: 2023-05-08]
Hardware/DPX_S2_Hardware/img/0_XPRO_S2.jpg

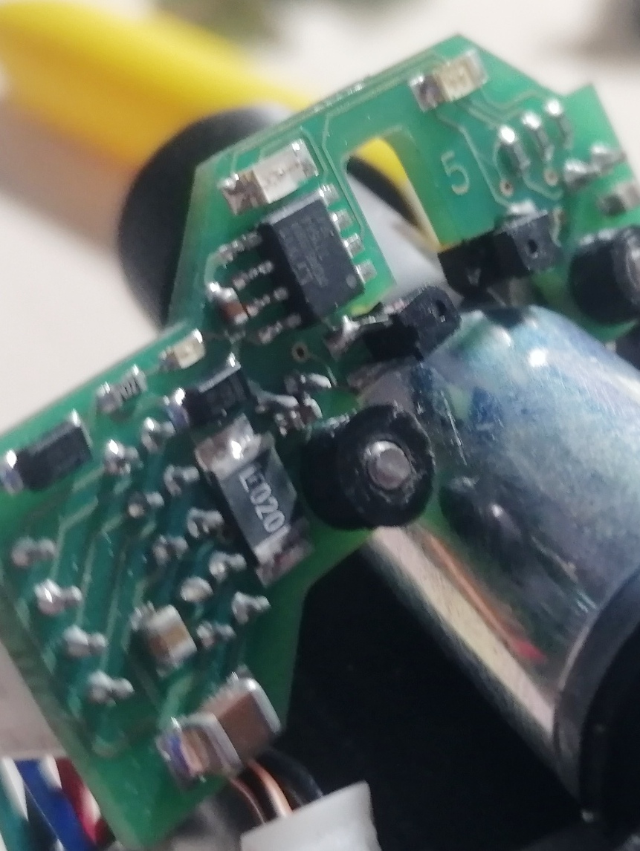
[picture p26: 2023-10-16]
Hardware/DES_Hardware/img/10_Picaso_Designer.jpg

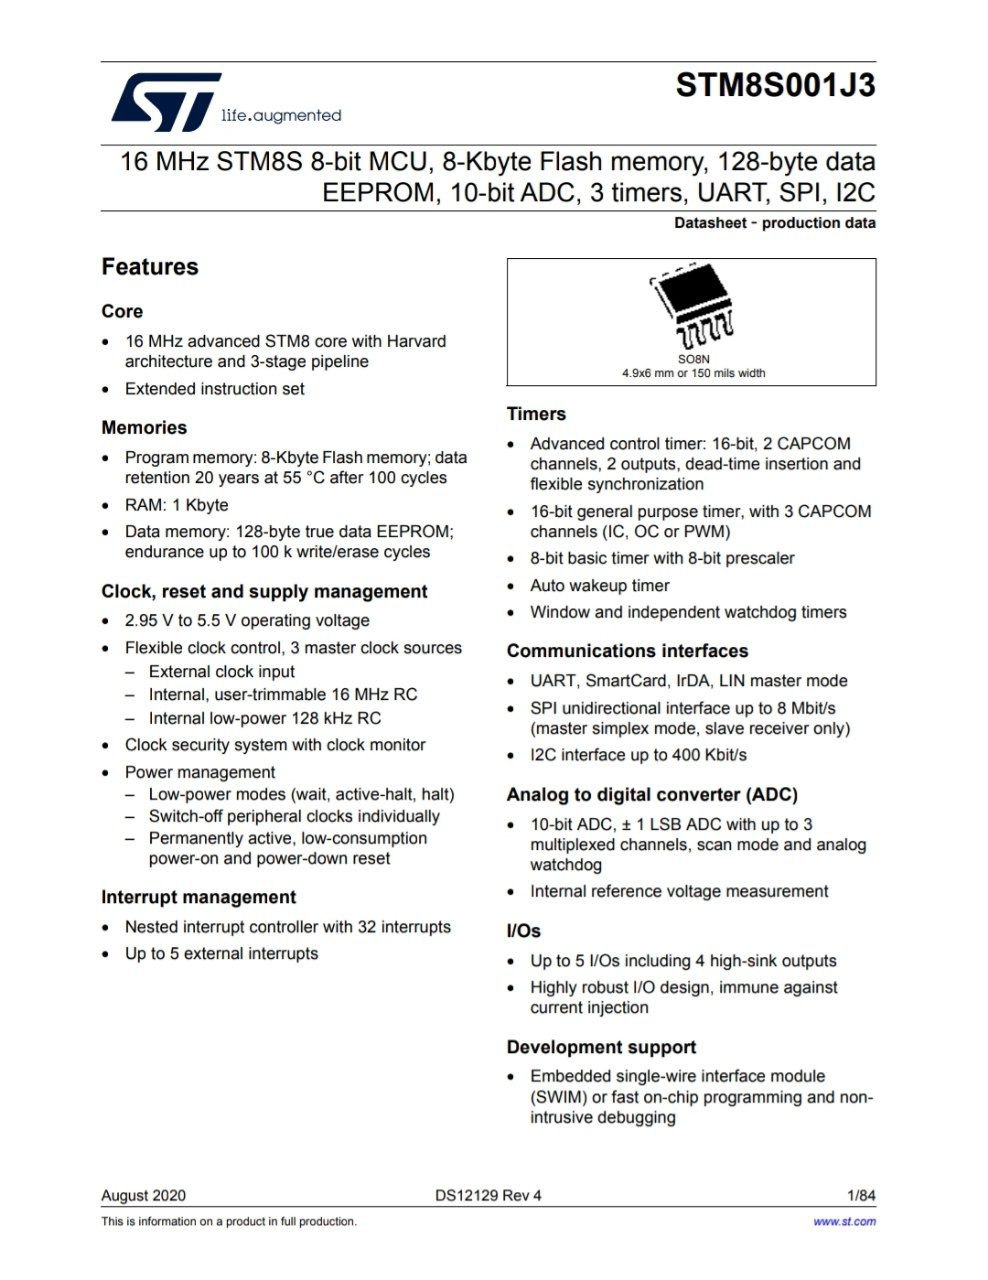
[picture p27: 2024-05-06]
Hardware/DXL_S2_Hardware/img/9_XL_S2.jpg

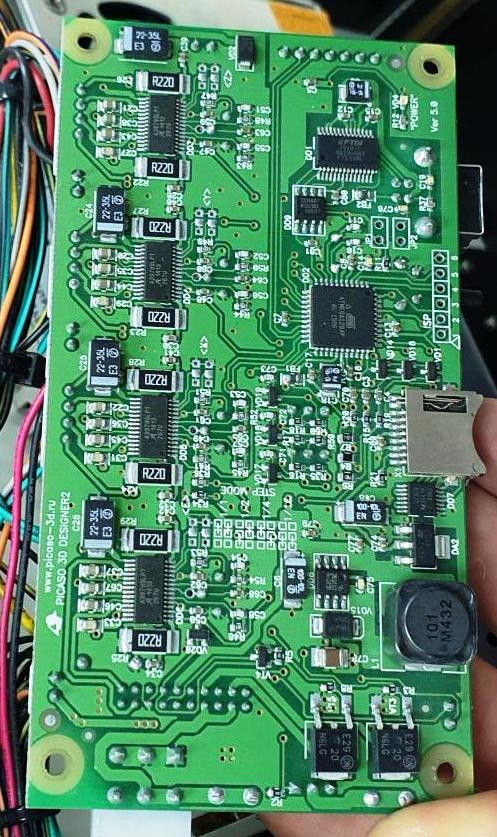
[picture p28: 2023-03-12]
Hardware/PRO250_Hardware/img/3_Picaso_PRO250.jpg

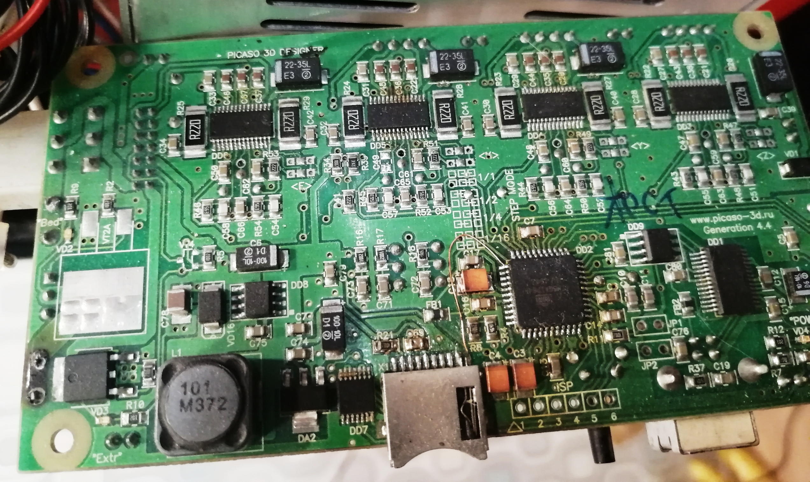
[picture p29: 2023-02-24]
Hardware/DES_Hardware/img/1_Picaso_Designer.jpg

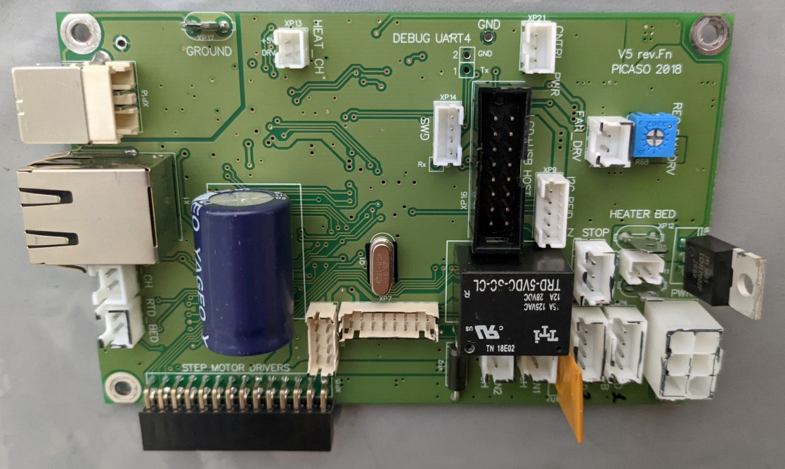
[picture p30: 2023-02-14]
Hardware/DPX_Hardware/DPX_Motherboard/img/0_XPRO_Motherboard.jpg

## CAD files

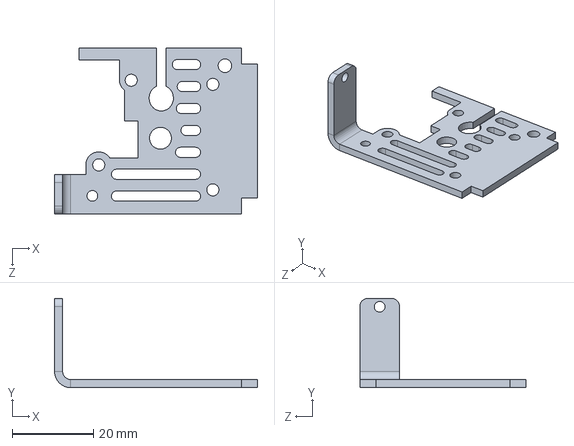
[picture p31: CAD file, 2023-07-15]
Hardware/DX_Hardware/DX_Радиатор.sldprt
50.0 x 22.0 x 41.0 mm

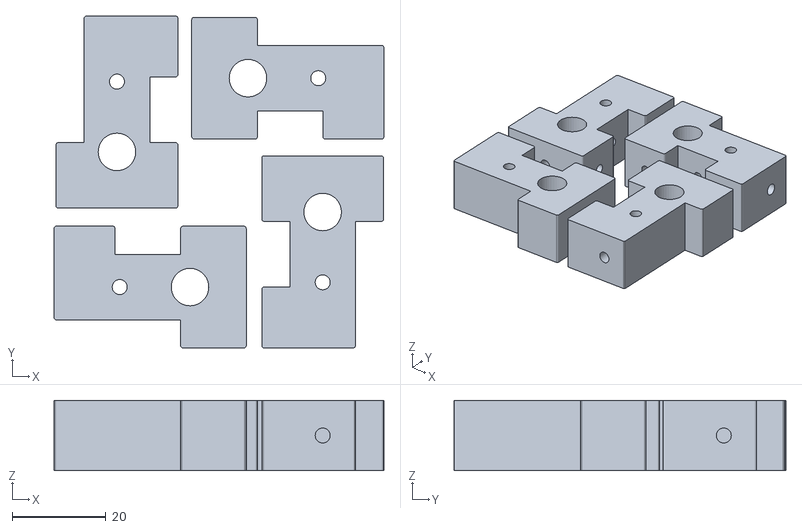
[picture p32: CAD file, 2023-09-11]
STL_Детали_принтеров/Designer/4_y_shaft.stl
70.4 x 70.8 x 15.0

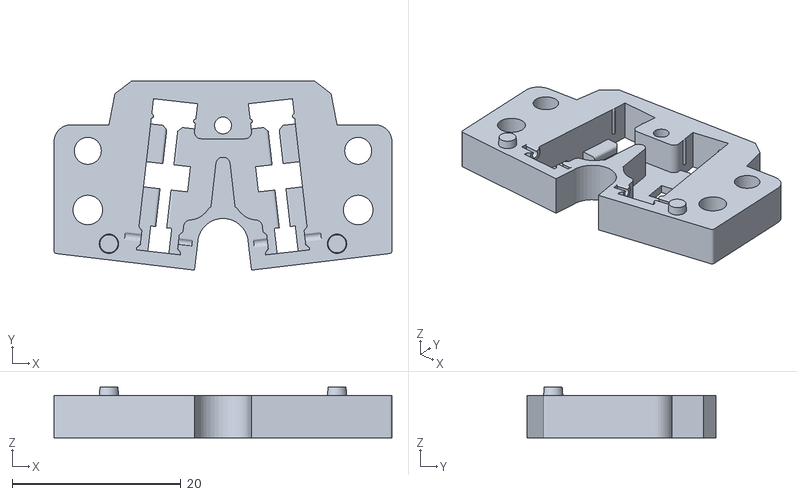
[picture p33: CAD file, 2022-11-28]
STL_Детали_принтеров/DPX_Блоки_энкодеров_S1_S2/DXPRO_Блок_энкодеров__S1/DXPRO_Крышка_блока_энкодеров_S1.stl
40.0 x 22.4 x 6.00

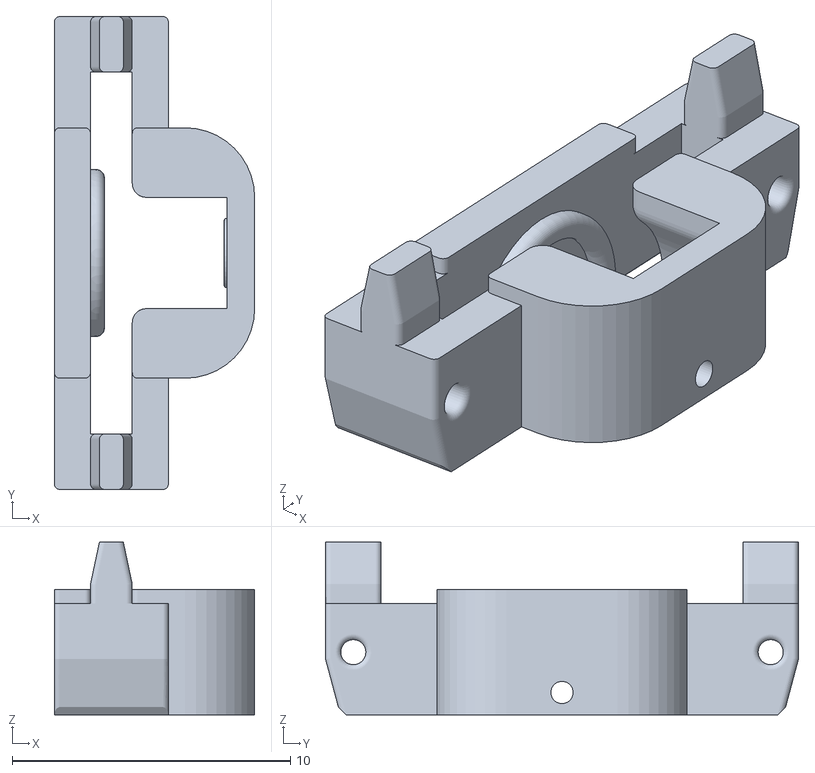
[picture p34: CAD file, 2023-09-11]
STL_Детали_принтеров/DX_DPX_Рычаг_диска_энкодера .stl
7.20 x 17.0 x 6.20

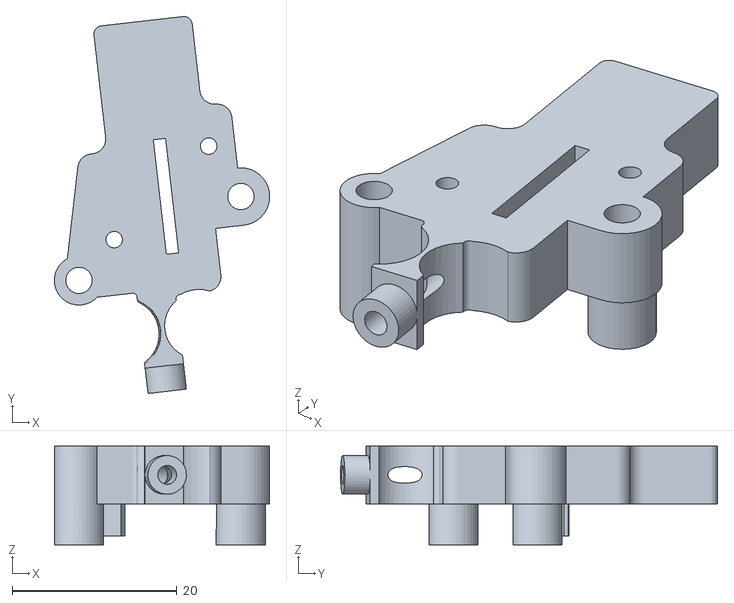
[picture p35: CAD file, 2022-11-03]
STL_Детали_принтеров/DX_Блок_энкодера_Корпус/DX_Блок_энкодера_004.11.01.STL
26.2 x 45.8 x 12.0

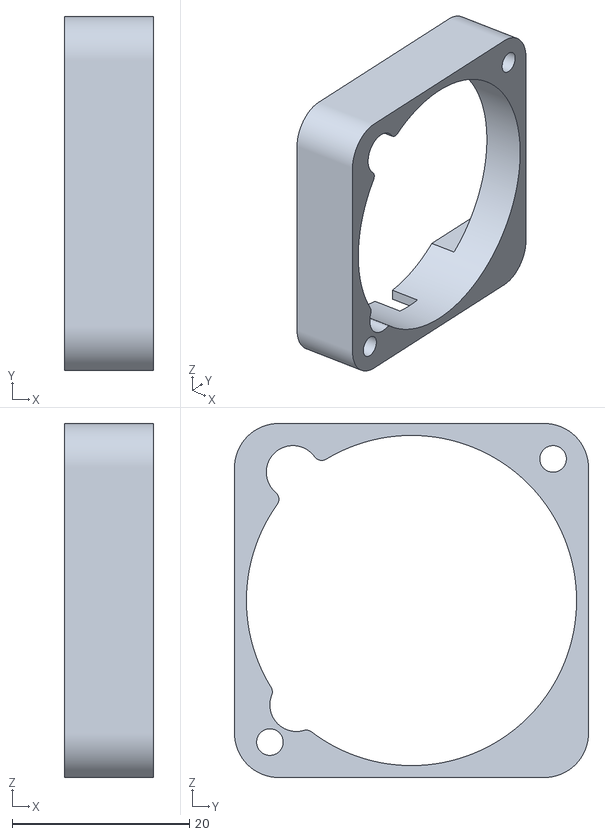
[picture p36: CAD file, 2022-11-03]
STL_Детали_принтеров/DX_Проставка_радиатора/DesX_Проставка_под_вентилятор_радиатора_.stl
10.0 x 40.0 x 40.0

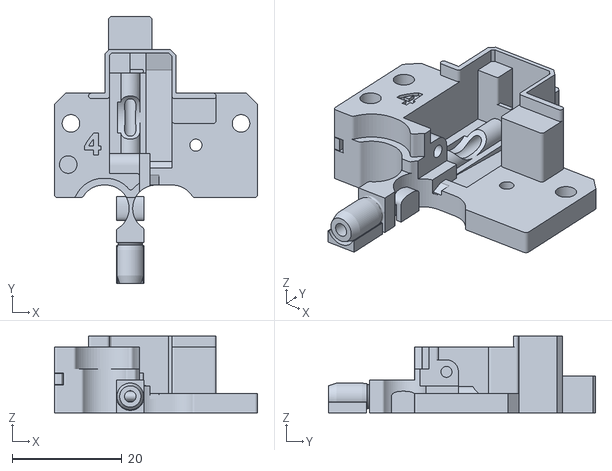
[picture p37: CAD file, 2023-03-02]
STL_Детали_принтеров/DXL_Блок_энкодера/DXL_Корпус_энкодера_старый.STL
37.0 x 48.7 x 14.0

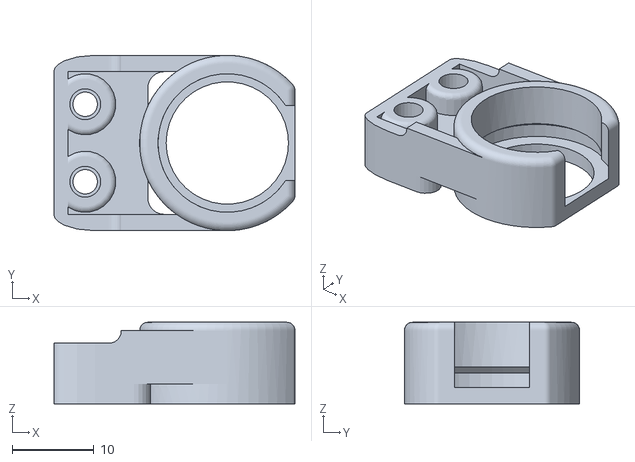
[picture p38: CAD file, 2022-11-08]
STL_Детали_принтеров/PRO250/PRO250_HolderUpgrade/Part2.stl
29.6 x 21.5 x 10.0

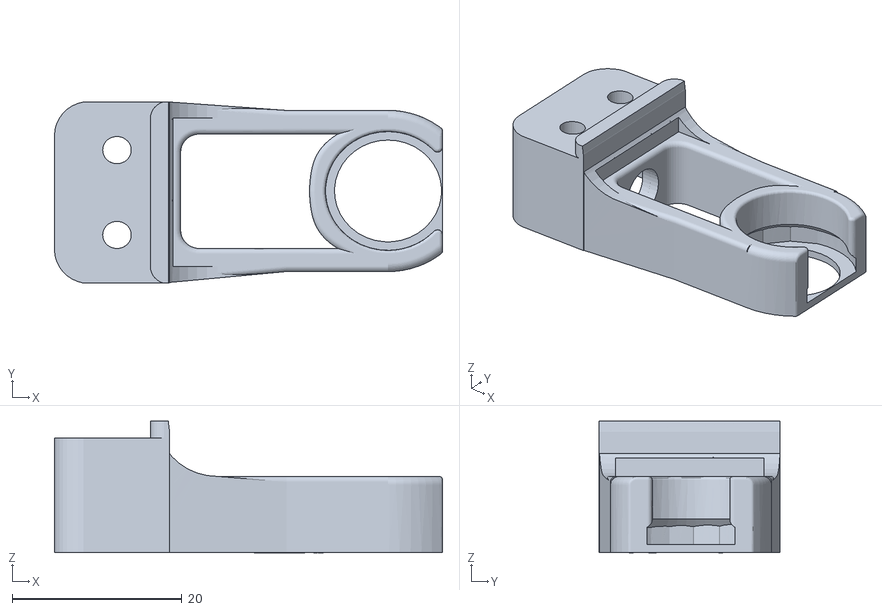
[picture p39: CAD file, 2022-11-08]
STL_Детали_принтеров/PRO250/Держатель_очистителя_PRO250_под_очиститель_X_PRO_repaired_fixed.stl
45.7 x 21.4 x 15.5

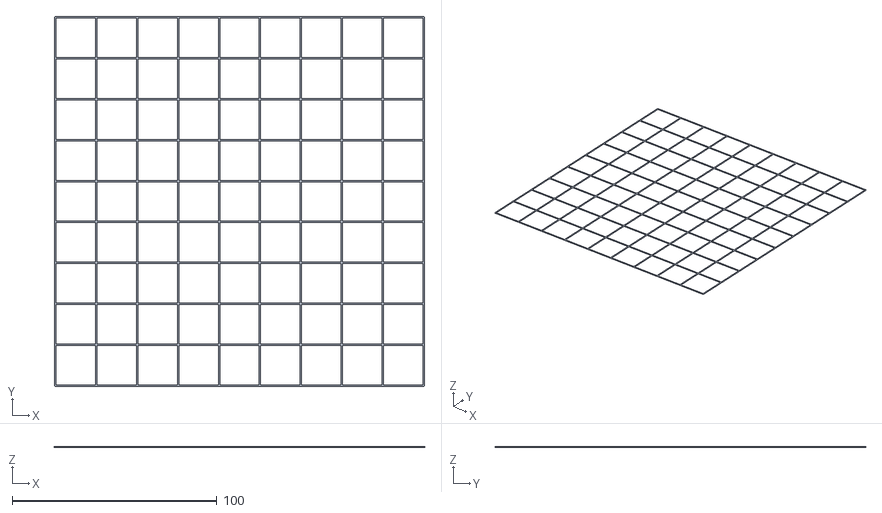
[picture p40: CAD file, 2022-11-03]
STL_Калибровочные_шаблоны/PRO250_Тест_ремней/18x18_Grid.stl
180.7 x 180.7 x 0.2

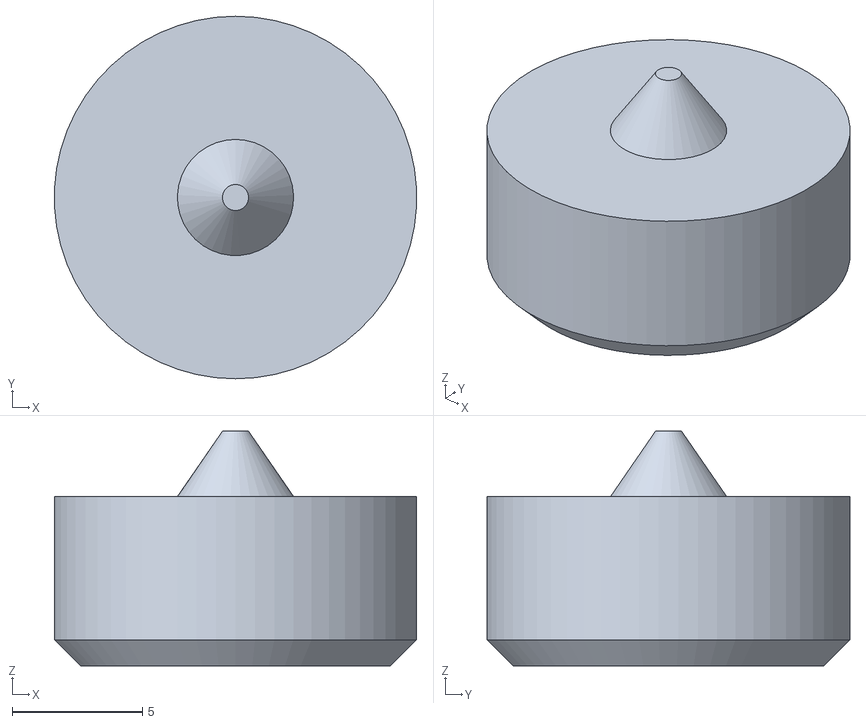
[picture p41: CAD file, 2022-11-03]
STL_Калибровочные_шаблоны/Калибровочный_шаблон_очистителя.stl
13.9 x 13.9 x 9.00

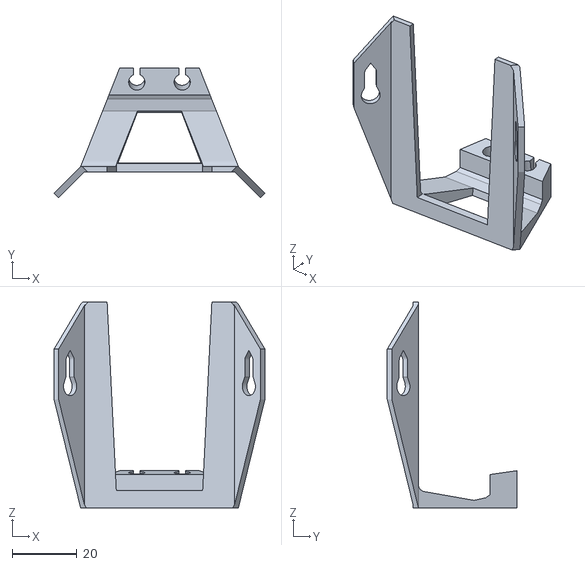
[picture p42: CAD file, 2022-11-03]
STL_Тюнинг/DPX_Фиксатор_трубок_подачи_пластика_mod3/DXPRO_Фиксатор_трубок_подачи_пластика_mod3.stl
65.0 x 39.9 x 63.5

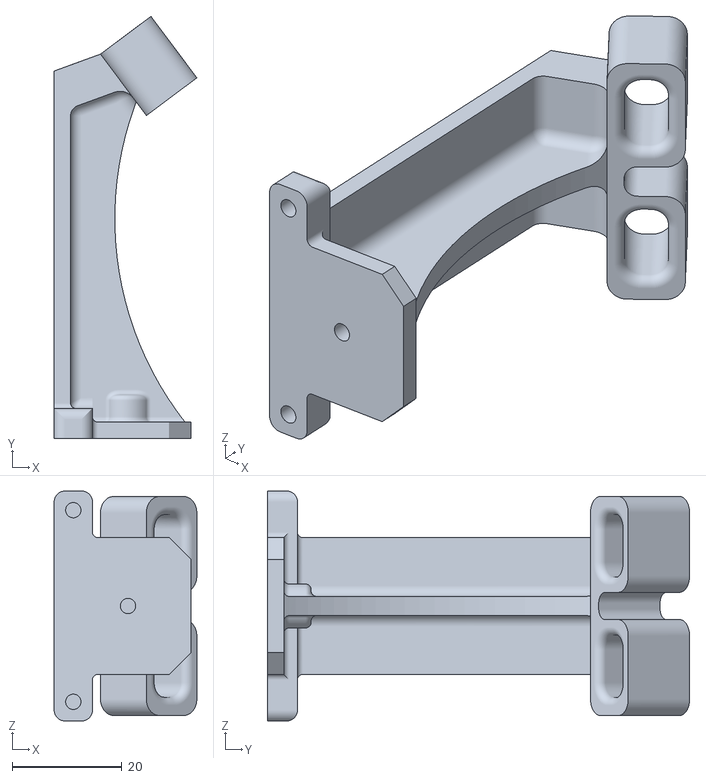
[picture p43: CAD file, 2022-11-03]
STL_Тюнинг/DPXL_Фиксатор_трубок_подачи_пластика/XLPRO_Фиксатор_трубок_подачи_пластика.STL
26.1 x 77.1 x 42.0

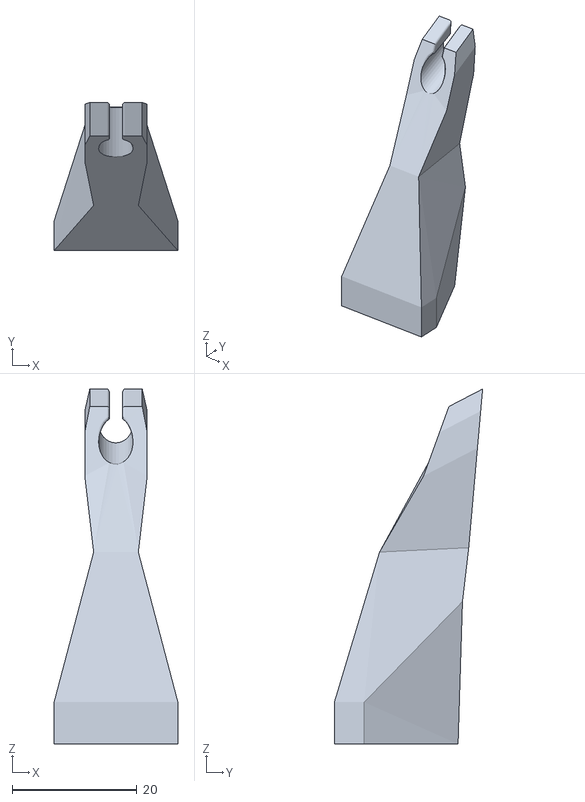
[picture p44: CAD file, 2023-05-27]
STL_Тюнинг/DX_S2_Фиксатор_трубок_подачи_пластика/X_S2_Фиксатор_трубки_подачи_v2.stl
19.8 x 23.7 x 56.8

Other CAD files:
STL_Тюнинг/DX_Вентиляторы_обдува_детали/4020_rear_fan_DX_mod.STL
STL_Тюнинг/DX_Фиксатор_трубок_подачи_для_Формакс/filament_tail.stl
STL_Тюнинг/DXL_DPXL_Крепление_стекла/Крепление стекла XL.SLDPRT
STL_Детали_принтеров/DES_Кронштейн.stl
STL_Детали_принтеров/DESС_00.00.03_Петля_верхняя_скрытая.STL
STL_Детали_принтеров/DESС_00.00.04_Петля_нижняя_скрытая.STL
STL_Детали_принтеров/DESС_00.00.06_Петля_средняя_скрытая.STL
STL_Детали_принтеров/DEX_Фиксатор_трубки_подачи_пластика.stl
STL_Детали_принтеров/DPS_004.10.09_Держатель_трубок.STL
STL_Детали_принтеров/DPS_01.00.14_Левый_зажим_эксцентрик.stl
STL_Детали_принтеров/DPS_01.00.14_Правый_зажим_эксцентрик.stl
STL_Детали_принтеров/DPS_02.00.02_01_Стойка_для_валов_XY.stl
STL_Детали_принтеров/DPS_02.00.08.01_Держатель_трубки.stl
STL_Детали_принтеров/DPS_02.00.08_01_Держатель_трубки_.stl
STL_Детали_принтеров/DPS_02.00.09_Держатель_чистика.stl
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

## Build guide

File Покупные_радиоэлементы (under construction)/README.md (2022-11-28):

# Покупные радиоэлементы для ремонта принтеров Picaso
---

1. IWISS IWS-3220 460PCS Crimping Pliers Mini Crimper Tool for JST DuPont Terminal Narrow-pitch Connector Pins 0.08-0.5mm²AWG 32-20

https://sl.aliexpress.ru/p?key=gGwexSX

2. Разъём PHD2.0 https://sl.aliexpress.ru/p?key=Jjtexmu

3. https://sl.aliexpress.ru/p?key=3zthxQy
Я первые поставил, натянув на них термоусадку, что бы не поцарапать стол снизу. После перехода на PEI стекло ни разу не снимал

4. Драйвер IXDN604SI https://aliexpress.ru/item/1005002628524804.html

5.  Loctite 601 620 648 680 https://sl.aliexpress.ru/p?key=s5b0Zo

6. Тефлоновая трубка 1 метр

+ https://a.aliexpress.com/_A3iYtX
+ https://aliexpress.ru/item/1005001661430005.html

7. Муфты:

+ https://aliexpress.ru/item/32903954998.html
 
+ https://a.aliexpress.com/_A3zzf6

+ https://aliexpress.ru/item/32888955522.html

+ https://aliexpress.ru/item/32915024956.html

PRO250_Драйвер_IXDN604SIA

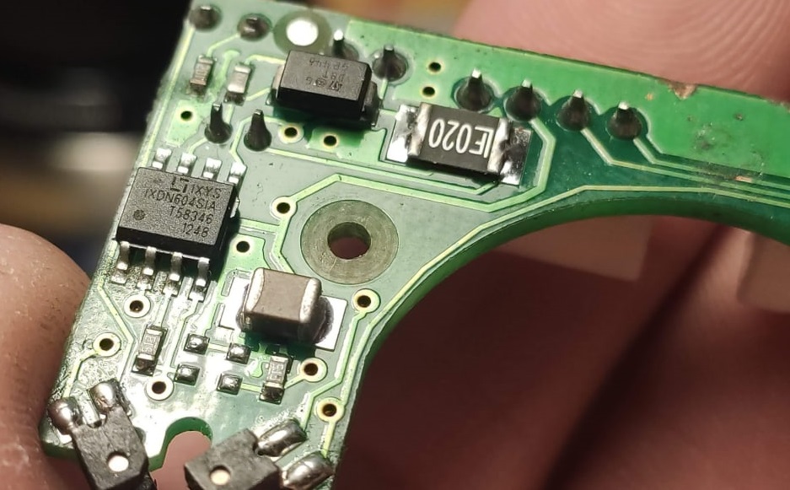
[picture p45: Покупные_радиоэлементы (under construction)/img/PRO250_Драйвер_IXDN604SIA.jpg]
PRO250_Драйвер_IXDN604SIA


XPRO_Мотор_охлаждения_детали.jpg

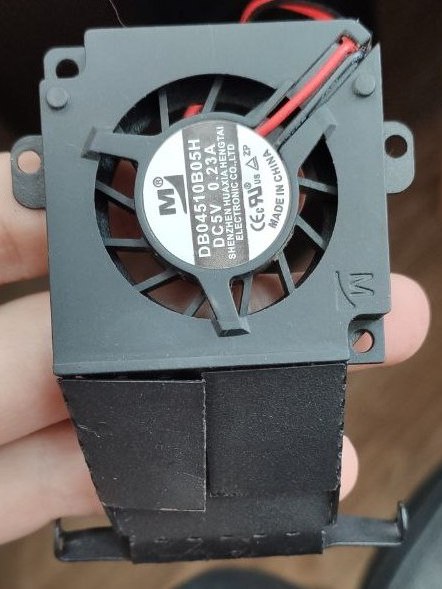
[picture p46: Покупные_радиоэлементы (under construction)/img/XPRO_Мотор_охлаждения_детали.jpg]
XPRO_Мотор_охлаждения_детали


XPRO_Транзистор_нагрева_сопла

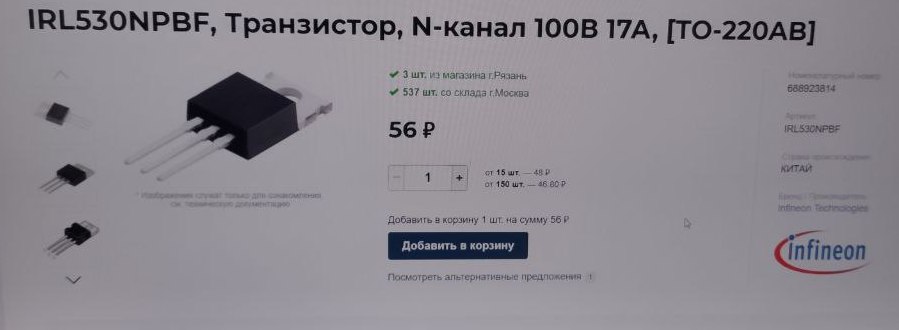
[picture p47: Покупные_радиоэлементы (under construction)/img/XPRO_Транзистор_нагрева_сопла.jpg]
XPRO_Транзистор_нагрева_сопла


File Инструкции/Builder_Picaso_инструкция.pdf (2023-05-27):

## Инструкция к 3D принтеру Picaso Builder

Содержание:

1. О принтере 3D Picaso Builder
2. Технические характеристики и требования
3. Меры безопасности
4. Установка программного обеспечения (Polygon for 3D Picaso Builder)
5. Подготовка к работе и печать на 3D Picaso Builder
6. Советы и правила эксплуатации
7. Советы по печати моделей STL
8. Сервис и поддержка

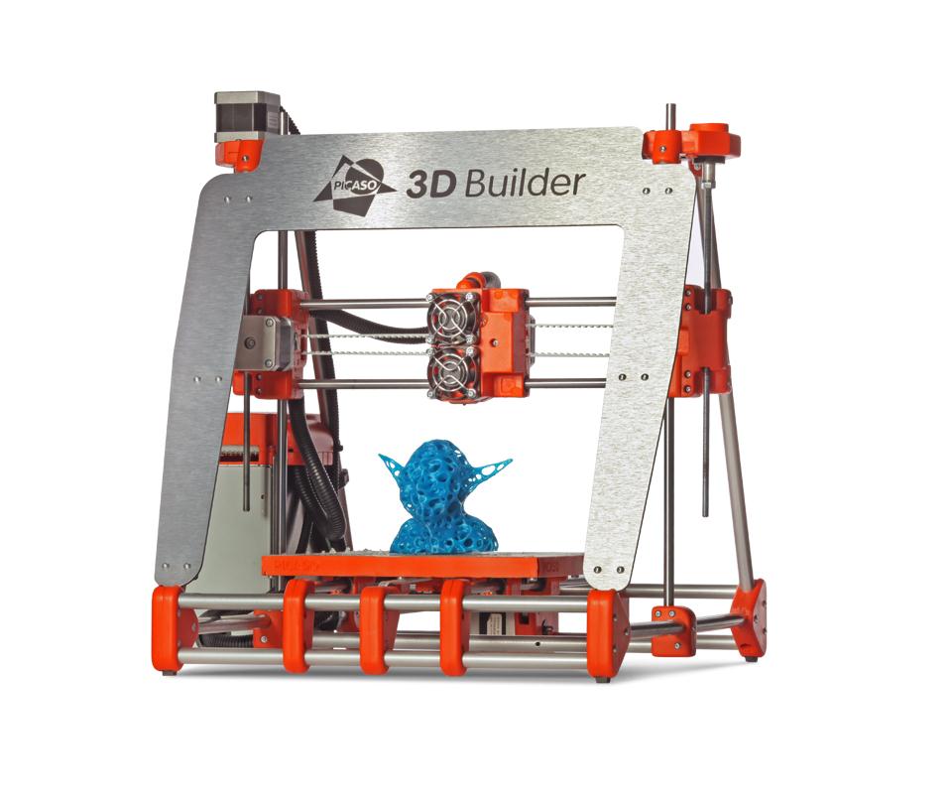
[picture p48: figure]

© 2013 FOTO-BUSINESS.RU / тел. 8 (499) 340-72-79

О принтере 3D Picaso Builder

Вы приобрели принтер 3D Picaso Builder – созданный в 2013 году российскими инженерами и полностью производимый в России. Благодарим Вас за выбор!

Наш принтер работает по технологии экструзии пластика – т.е. модель получается путем послойного нанесения тончайших слоев расплавленного пластика. Готовые изделия при этом получаются точными, практичными и прочными. Для печати используются АБС и ПЛА (ABS \ PLA) пластики, отвечающие требованиям безопасности и практичности. Их можно обрабатывать, сверлить, шлифовать и окрашивать. Сейчас производители пластиков внедряют все новые виды и разновидности этих пластиков обладающие новыми интересными свойствами (например: светящиеся, сверхпрочные, водорастворимые, гибкие и т.д.). Вы также сможете создавать модели из них на вашем 3D Picaso Builder, по мере их появления в продаже и тестирования нашими специалистами. Более подробную информацию по этому вопросу Вы всегда найдете на нашем сайте www.foto-business.ru

Подробнее о 3D Picaso Builder. Как мы уже сказали – это очень современный 3д принтер, созданный в 2013 году и имеющий ряд неоспоримых преимуществ. При этом работы над усовершенствованием принтера продолжаются и дальше – Вы сможете производить апгрейд вашего 3D Picaso Builder и получать новые возможности как в механической части, так и в программной.

Ключевые особенности и преимущества 3D Picaso Builder:

- Поддержка в России, специалисты, технические консультанты и обучение.
- Принтер полностью адаптирован для работы пользователем, не требуется специальных навыков.
- Поставляется собранным, настроенным и протестированным. Вам не придется настраивать ни программу, ни калибровать сам принтер.
- Нет проблем с застреванием и подачей пластика при печати.
- Прочная печатная платформа, которая не перекашивается и не выгибается в процессе эксплуатации.
- Превосходная адгезия (прилипание) пластика к печатной платформе. Модель не отлипает и не загибается в процессе печати.
- Высокое качество печати. Толщина слоя от 0,25 до 0,05 мм!

Для работы принтера используется специальная программа Polygon, в которую Вы загружаете модели в формате файлов STL (сохраняются из любого 3D редактора). Она поставляется вместе с принтером, а так же Вы всегда можете скачать свежую версию с нашего сайта. Программа сделана с учетом всех особенностей эксплуатации, при этом она простая, естественно на русском языке и Вам не потребуется много времени на ее освоение. В среднем на «понимание» программы уходит не более 20 минут после прочтения инструкции. Все функции логичны и интуитивно понятны. У Вас не будет трудностей, даже если Вы до этого никогда не работали с 3д принтерами.

В итоге – с 3D Picaso Builder Вы сможете создавать прочные и детализированные прототипы, использовать его для мелкосерийного или штучного производства деталей, воплощать любые творческие задачи или продавать услуги по воплощать любые творческие задачи или продавать услуги по 3D печати из пластика.

Технические характеристики и требования

Питание | 220 В.
Потребляемая мощность | 300-350 Вт.
Используемые виды пластика | АБС и ПЛА
Толщина используемой нити | 1,75 мм.
Толщина слоя печати | 0,05 – 0,250 мм.
Диаметр сопла печати | 0,15 \ 0,30 мм.
Минимальная толщина печатаемой стенки | 0,19 мм.
Область печати | 200 х 200 х 200 мм.
Формат файлов для печати | STL
Подключение к ПК | USB
Скорость печати | до 25 см3\час.
Печатный стол | подогреваемый
Габариты принтера | 470x422x441 мм.
Вес принтера | 6,5 кг.

Требования к компьютеру:

- Многоядерный процессор (не менее 2-х ядер), с частотой не менее 1,6 Ггц.
- Оперативная память – не менее 2 Гб. Для генерации больших моделей с высоким разрешением потребуется до 8 Гб.
- Операционная система Windows XP, 7, 8 (рекомендуется 64 разрядная система).

Меры безопасности

- Используйте 3D принтер только в стандартных сетях переменного тока 220 В.
- Не используйте принтер с поврежденным или не оригинальным кабелем питания.
- Работа принтера сопряжена с высокими температурами и вращающимися механизмами, поэтому не допускается использование принтера детям без присмотра квалифицированных взрослых.
- Не приближайтесь к принтеру с: длинными распущенными волосами, галстуками, наушниками и т.д. Во избежание попадания этого в движущиеся и вращающиеся элементы принтера!
- Не прикасайтесь к принтеру во время печати во избежание ожогов и повреждений. Печатающий стол во время печати может достигать температуры 110 С, экструдер (печатающая головка) – 270 С.
- Принтер должен стоять на ровной устойчивой поверхности, вдали от легковоспламеняющихся веществ, открытого огня, источников воды, увлажнителей и пр.

- Принтер предназначен для использования в комнатных условиях со стандартной температурой и влажностью. Не используйте его вне помещений, на открытом воздухе или вблизи с открытыми окнами.

Установка программного обеспечения (Polygon for 3D Picaso Builder)

Для эксплуатации 3D принтера Picaso в комплект поставки входит программа Polygon на русском языке. Она удобна и проста в эксплуатации.

Для установки ПО на ваш компьютер необходимо запустить установочный файл или скопировать папку POLYGON FOR 3D Builder на жесткий диск.

Внимание: во избежание проблем с работой ПО рекомендуется устанавливать его на жесткий диск С, в корневую папку, на компьютере с операционной 64 разрядной системой Windows.

В случае если Вы все же используете 32 разрядную систему, то необходимо заменить содержимое папки «Slic3r» на содержимое архива «slic3r-mswin-x86-0-9-8.zip».

Для запуска программы используйте файл Polygon.exe

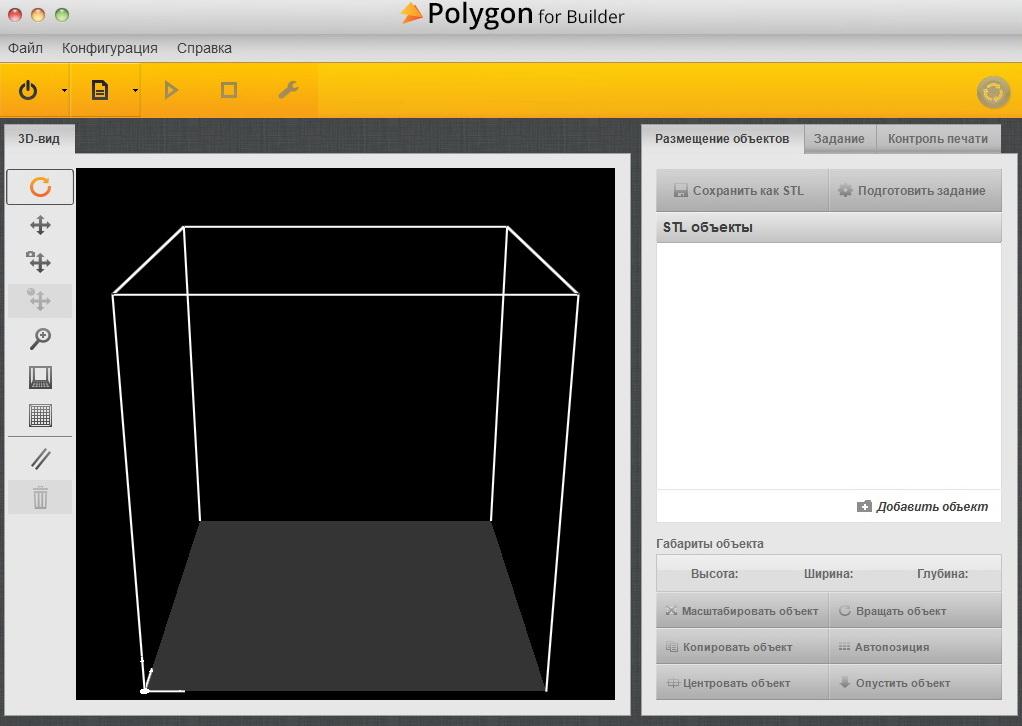
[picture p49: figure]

После установки программы, подключите принтер через USB шнур, входящий в комплект. Включите питание принтера. Далее на большинстве систем произойдет автоматические подключение нового устройства, при условии, что компьютер подключен с сети Интернет.

Внимание: если у Вас не произошло автоматической установки – скачайте в Интернете драйвер FTDI для вашей версии операционной системы и установите его.

Далее запустите программу Полигон и выберите меню Конфигурация -> Настройки принтера

Выберите СОМ порт на который подключился принтер (в примере это СОМ8). Название принтера можете написать самостоятельно на свое усмотрение. Нажмите кнопку сохранить. См. ниже:

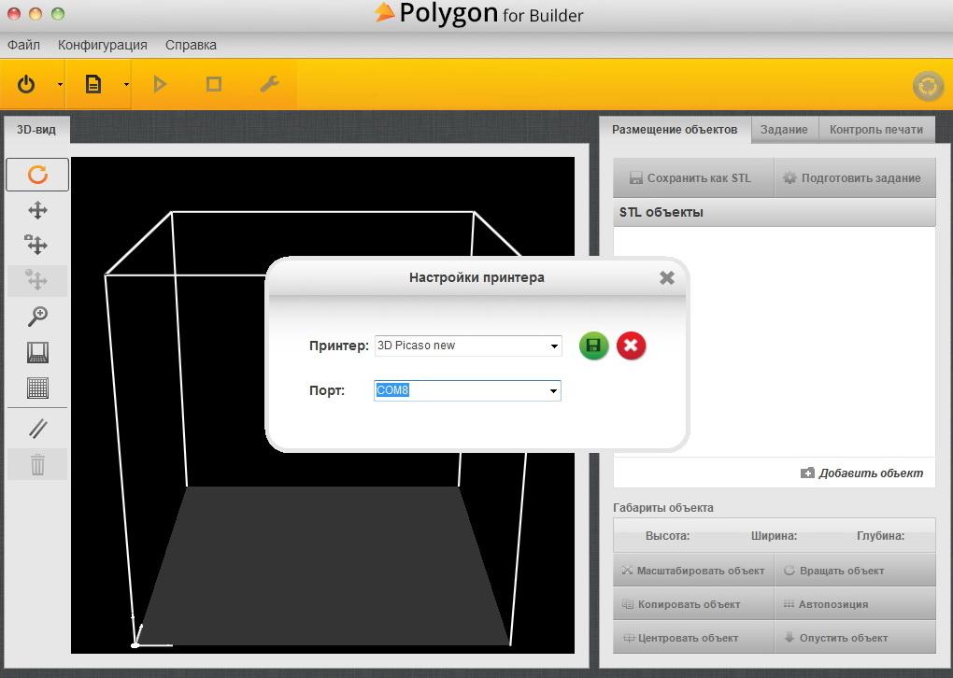
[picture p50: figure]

При включенном принтере, нажмите кнопку включение принтера:

и он подключится к программе, кнопка станет зеленой.

Все – установка принтера выполнена, Вы можете приступать к работе и печати на нем!

Подготовка к работе и печать на 3D Picaso Builder

Этап 1 - Наклейка пленки для печатной платформы

Для лучшего прилипания к печатной платформе используется специальная самоклеящаяся пленка. Так же Вы можете использовать для этих целей «Самоклеющуюся пленку для лазерных принтеров» (глянцевую или матовую).

Приклейте пленку на платформу и обрежьте края канцелярским ножом. Если на пленке образовались пузырьки – проткните их иголкой и выпустите воздух из под пленки.

После наклеивания пленки, а так же перед каждой печатью рекомендуется обезжиривать ее поверхность протерев спиртом.

Советы:

- для более удобного наклеивания пленки, Вы можете поднять печатающую головку вверх и выдвинуть платформу максимально вперед. Это можно сделать в Сервисном режиме, выбрав ручное управление.
- для легкого отклеивания старой пленки (когда она уже повреждена), выберите в режиме ручного управления нагрев платформы до 70 С. После снятия пленки – протрите следы клея спиртом или другим легким растворителем.

Вид окна ручного управления:

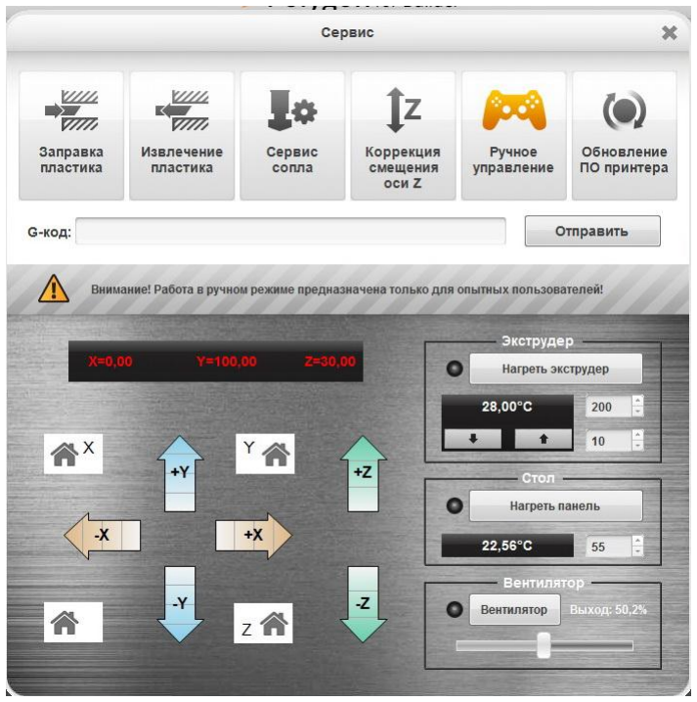
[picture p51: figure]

Этап 2 - Заправка пластика

Подготовьте бобину с пластиковой нитью, установите ее на подставку, подрежьте конец нити, чтобы он был ровный. Не допускается использование непроверенных производителем нитей, грязных, изломленных, поврежденных и т.д. Это может вывести принтер из строя и потребовать ремонта или обслуживания в сервисном центре.

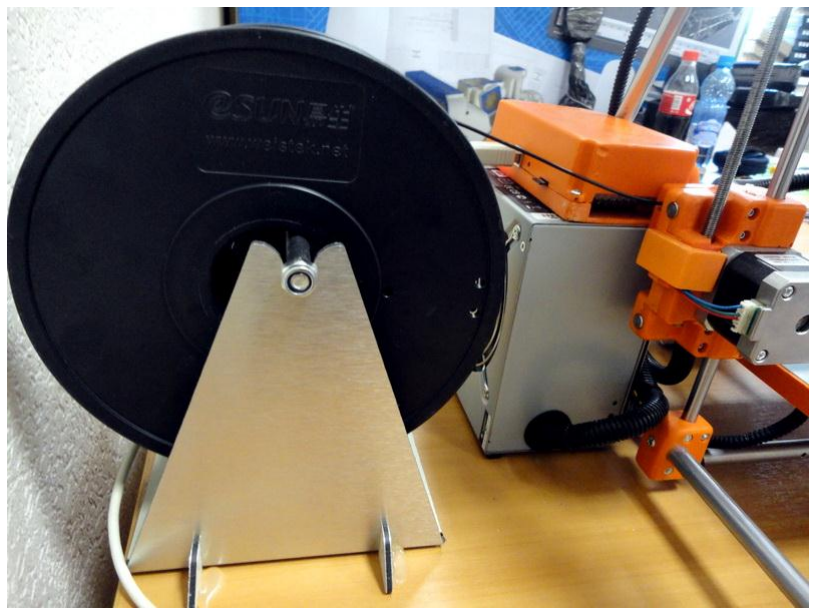
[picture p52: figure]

Конец нити заправьте в отверстие для подачи сбоку принтера. См. фото:

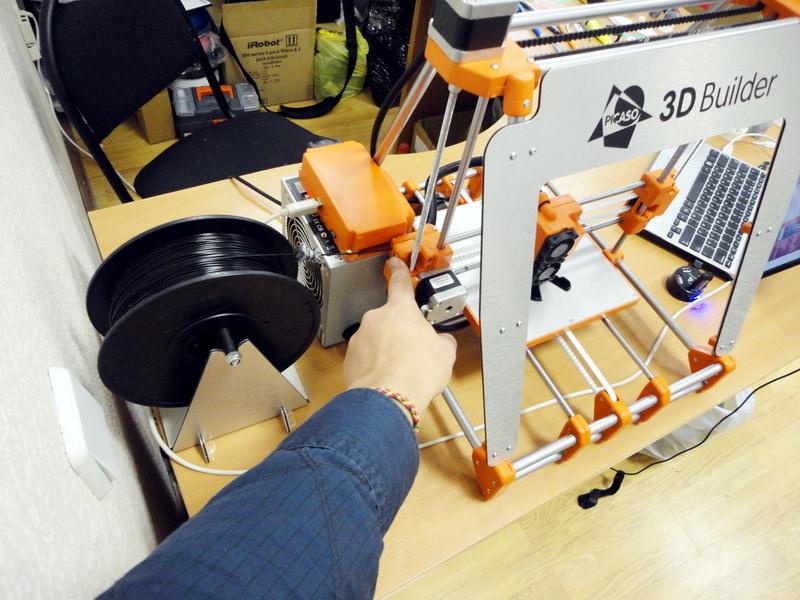
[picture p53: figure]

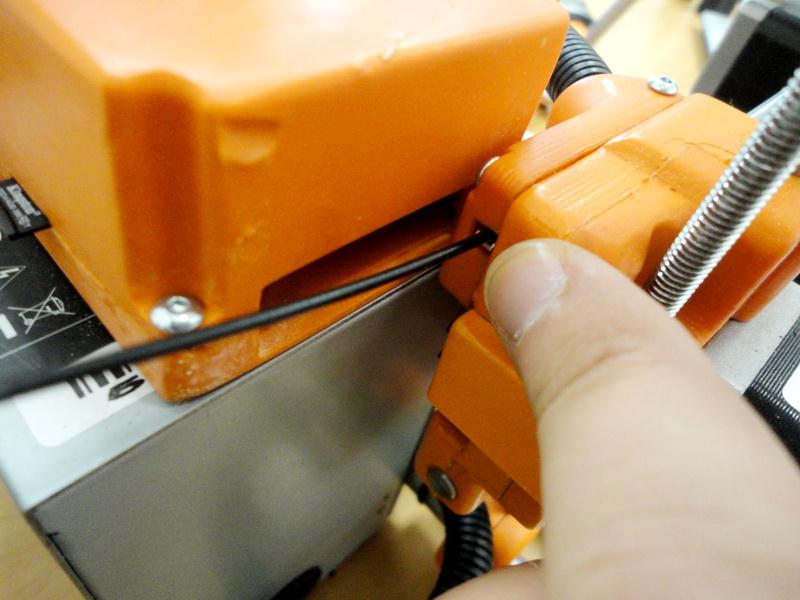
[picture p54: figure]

Далее пропихните около 30 см нити до момента, пока нить не упрется в экструдер.

Нажмите кнопку «Сервис» и выберите режим «Заправка пластика». После этого принтер проверит центровку и выйдет в позицию для заправки. В этот момент слегка поддавливайте нить вперед. Вы почувствуете как она потихоньку поползла вперед и затягивается экструдером. Через несколько секунд из экструдера начнет выдавливаться тонкая расплавленная нить пластика. После этого можете нажать кнопку Стоп. Нить еще будет выползать 10 секунд и процесс заправки можно считать завершенным. Если до этого Вы использовали другой цвет нити, подождите, пока цвет полностью сменится на новый и нажмите кнопку Стоп.

Вид окна «Сервис»:

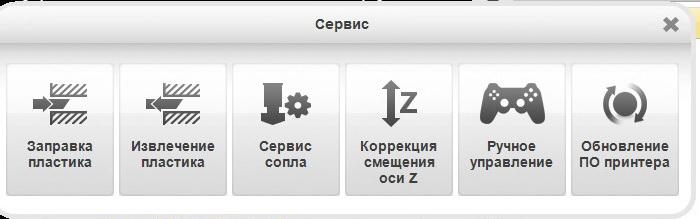
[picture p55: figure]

Совет: При смене пластика – не забывайте выбрать нужный тип (ПЛА или АБС) в настройках при генерации задания!

Внимание: При заправке или извлечении пластика принтер производит калибровку и касается разогретым соплом платформы. Поэтому на платформе не должно стоять предметов, моделей и пр.

Извлечение пластика:

Для смены пластика нажмите кнопку «Сервис» – «Извлечение пластика». После этого принтер произведет калибровку, встанет в положении замены и начнет выдавливать нить назад.

В этот момент Вы должны держать нить рукой и как только почувствуете обратных ход нити, немедленно сильно потянуть ее и вытащить полностью из принтера.

Внимание: Если Вы не вытащите нить пластика в момент срабатывания принтера на извлечение, нить может заплавится и застрять в экструдере. Будьте внимательны. Не пропустите момент вытаскивания нити и с силой вытяните ее из принтера.

Смена сопла производится ключом, который входит в комплект поставки. Перед сменой сопла нажмите «Сервис» и «Сервис сопла». Принтер разогреет его и Вы сможете легко открутить и поменять сопло. Будьте аккуратны – сопло при откручивании сильно разогрето! Не закручивайте сопло с большой силой!

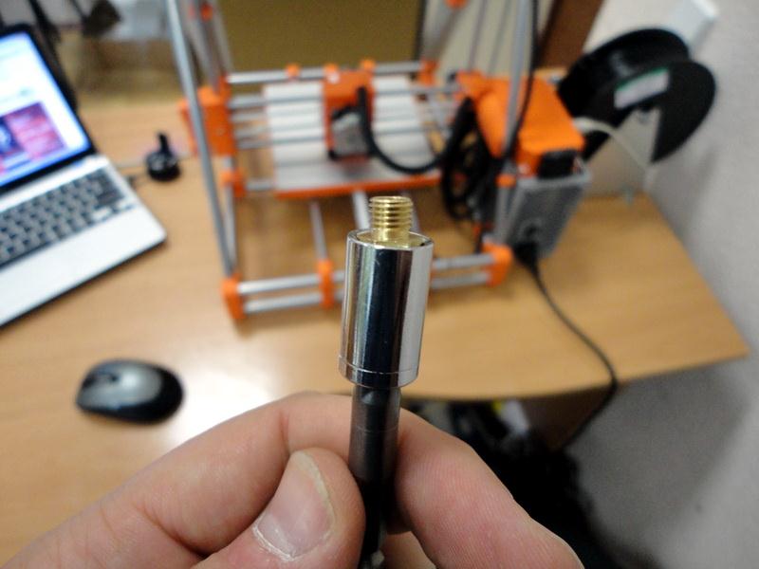
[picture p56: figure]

Этап 3 – Загрузка модели в ПО принтера

Для загрузки модели, выберите STL файл и перетащите его мышкой на окно программы Polygon.

Модель загрузится и Вы увидите ее отображение:

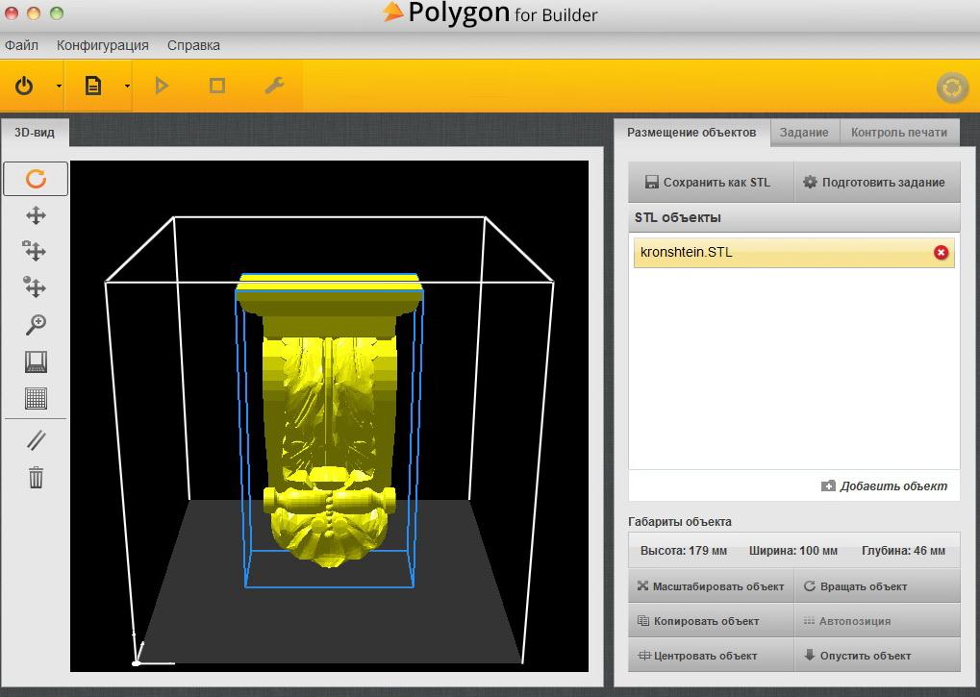
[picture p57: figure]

Совет: для стабильной работы программы избегайте кириллицы в названиях файлов моделей.

После того как Вы загрузили модель, можно:

- выбрать масштаб (модель можно печатать в натуральную величину или уменьшить\увеличить ее). Для этого используйте кнопку «Масштабировать объект».
- можно вращать модель и разместить ее так, как будет лучше для качества печати (кнопка «Вращать объект»).
- можно создать несколько копий объекта и напечатать не одну деталь, а столько, сколько поместится на платформе. При этом программа сама расставит их по платформе. Кнопка «Копировать объект».

После того как Вы разместили объект – можете приступать к следующему шагу и генерировать задание.

Этап 4 – Выбор параметров и генерация задания (G-кода)

Нажмите кнопку «Подготовить задание» и появится окно параметров генерации:

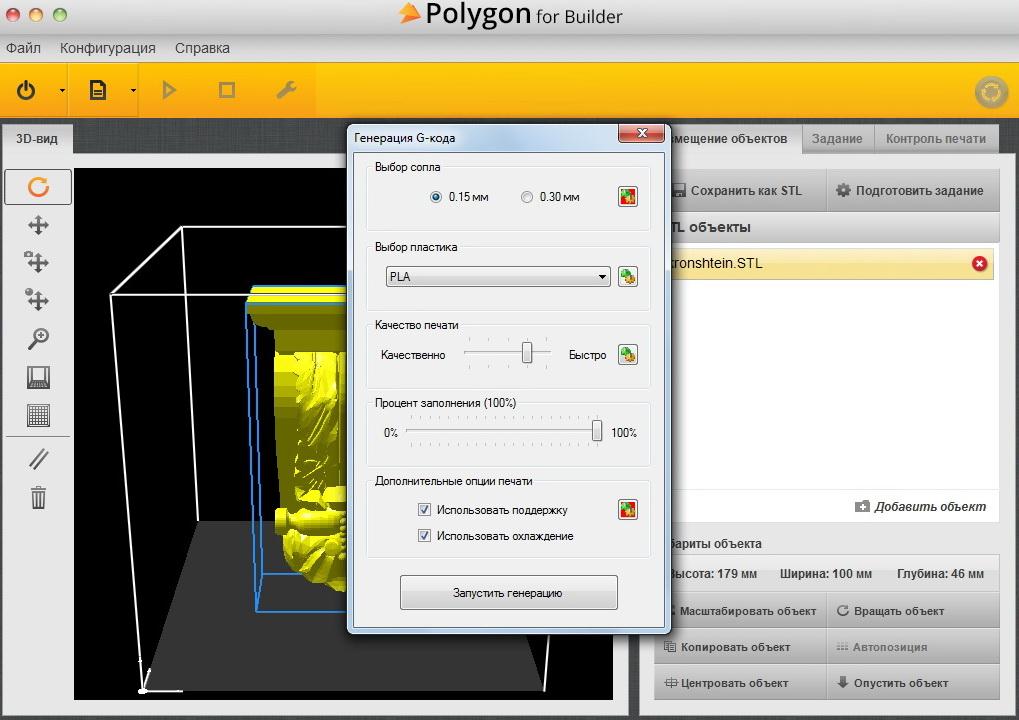
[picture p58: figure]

Вам нужно выбрать:

- Тип установленного сопла (0,30 – для быстрой печати, 0,15 для сверхточной печати). Для каждого сопла Вы также можете выбрать толщину слоя печати, кликнув на маленькую иконку справа от выбора диаметра сопла.
- Тип используемого пластика (ПЛА или АБС).
- Качество печати: это баланс между скоростью печати и качеством. Выбирается в зависимости от ваших предпочтений.
- Процент заполнения: указывает что принтер будет делать с пустотами в модели. Указав 0%
- модель будет полая, будут напечатаны только стенки каркаса. 100% - сделают модель полностью литой, все пустоты принтер заполнит пластиком на 100%. А так же Вы можете выбрать любой другой процент заполнения, тогда принтер заполнит пустоты сетчатой структурой, наподобие сот. Модель будет легче, расход пластика сократится. Если Вам нужно что бы модель была достаточно прочной и легкой – советуем выбирать небольшой процент заполнения от 10 до 30%. Для деталей от которых нужна прочность – процент заполнения должен стремиться к 100.
- Использование поддержек: для некоторых моделей, у которых есть свисающие элементы, принтеру будет нужно поставить поддержки. Например пирамиду – Вы можете печатать без поддержек, новые слои будут ложиться на предыдущие. А вот если печатать мост – то нужно поставить поддержки. Т.к. принтер не может напечатать пластиком висящие в воздухе элементы. Выбрав галочку в этом пункте – программа сама расчитает и сделает поддержки. Однако Вы можете варьировать параметры поддержек: например угол наклона детали, начиная от которого программа поставит поддержки; частоту поддержек – как часто будут расположены поддержки (подбирается опытным путем, по умолчанию 1,5 мм.).
- Использовать охлаждение: для печати тонкостенных моделей и объектов с мелкими элементами (например мост с тонкими перилами).

Далее нажмите «Запустить генерацию» и программа начнет генерировать G-код. Этот процесс может занять от нескольких секунд до нескольких минут (зависит от детализации модели, толщины слоя и мощности вашего ПК).

Внимание: Обратите внимание, что для сложных моделей, печатаемых тонким слоем – нужен очень производительный ПК с большим объемом оперативной памяти!

Этап 5 – Печать 3D модели

После генерации G-кода, Вы увидите примерно следующую картинку:

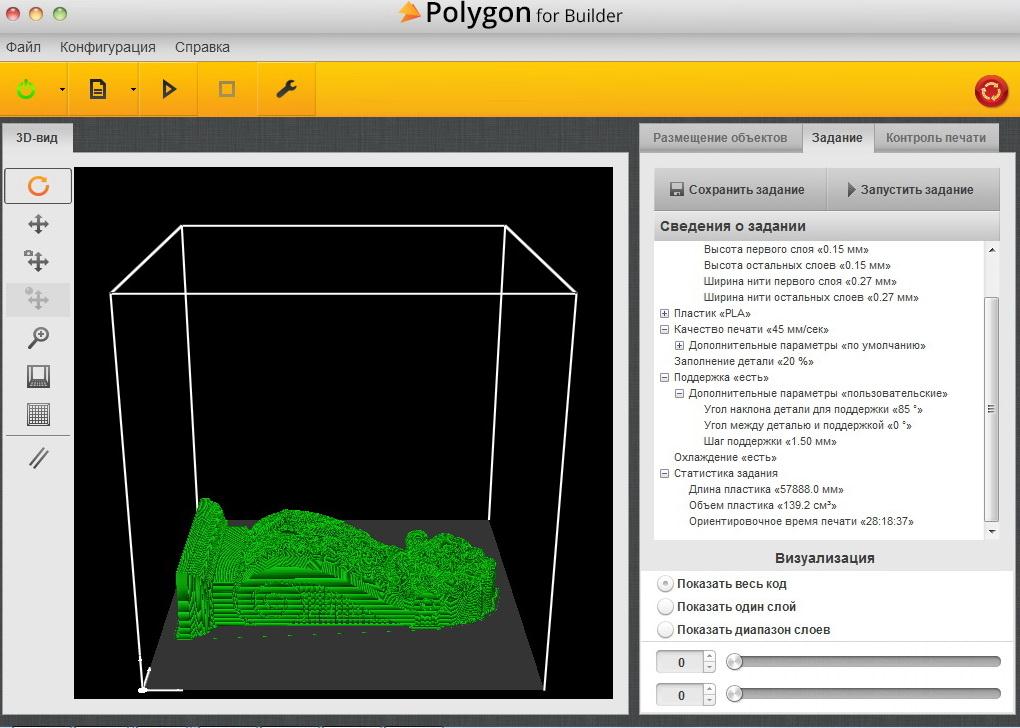
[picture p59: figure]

Модель будет отображаться зеленым цветом, приблизив картинку будут видны слои пластика – это то, как принтер будет послойно «выращивать» модель.

Справа Вы увидите параметры печати, тут можно все еще раз перепроверить.

На этом этапе Вы можете сохранить задание в виде G-кода, для того что бы потом не генерировать все заново, если потребуется напечатать еще одну такую же модель с теми же параметрами. Так же G-код нужно сохранять для печати с принтера через микро-СД карту.

Нажмите кнопку «Запустить задание»:

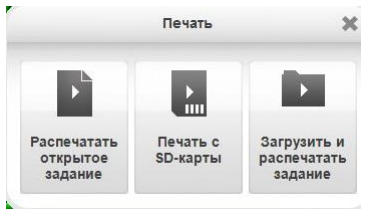
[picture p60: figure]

Для того, чтобы печатать с ПК – нажмите «Распечатать открытое задание». При этом все время печати ваш компьютер должен быть включен, «спящие режимы» ПК должны быть выключены!

Если Вы хотите включить принтер автономно – нажмите «Печать с SD-карты». При этом варианте Вам нужно предварительно записать сохранённый G-код на карточку (входит в комплект), подключив ее к ПК, а потом воткнуть ее в слон на плате принтера. При нажатии на «Печать с SD-карты», откроется менеджер карточки которая сейчас воткнута в принтер, там Вы выбираете нужный G-код и нажимаете печать. После того как принтер начнет работу – можете отключать USB кабель и убирать \ выключать компьютер. Принтер будет выполнять G-код автономно.

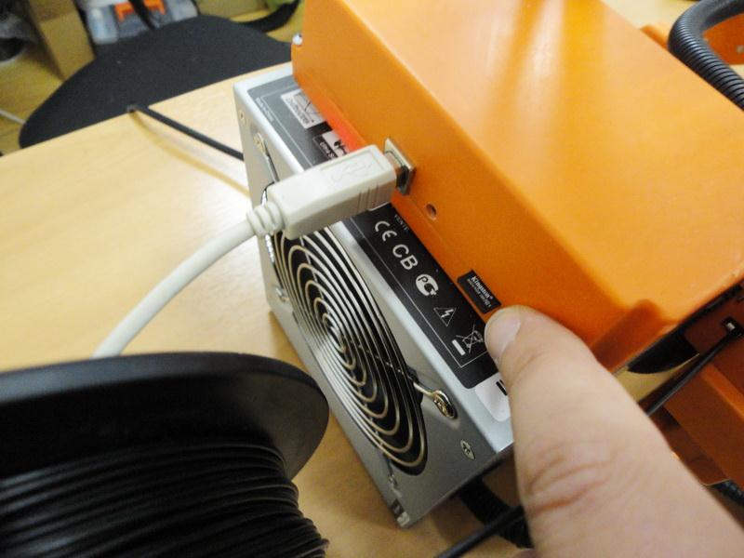
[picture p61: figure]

Обратите внимание, что G-код лучше сохранять в названии с латинскими буквами!

Так же Вы всегда можете открыть G-код и распечатать его.

Советы и правила эксплуатации

- Следуйте рекомендациям по технике безопасности, описанным в начале инструкции. Это обезопасит Вас и сохранит принтер в рабочем состоянии.
- Любые конструктивные изменения в принтере, механические вмешательства – повлекут снятие принтера с гарантии.
- В случае использования сторонних пластиков, не проверенных производителем принтера, мы не гарантируем качественную печать и сохранность работы принтера. Учитывайте, что у некоторых производителей качество пластика сильно отличается, а самое главное – может варьироваться толщина. В этом случае пластик застрянет в экструдере и принтеру потребуется сервисное обслуживание.
- Готовую модель можно клеить, шкурить, сверлить и обрабатывать механически. Для придания модели максимальной гладкости покрытия – можно обработать ее подходящим растворителем.
- Модели могут быть окрашены. Рекомендуем матовые быстросохнущие акриловые краски в баллончиках (из автомагазина). В некоторых случаях может потребоваться предварительная грунтовка.

Советы по печати моделей STL

- Некоторые программа не совсем корректно конвертируют и сохраняют STL формат файлов. Советуем внимательно подойти к этому вопросу и детально изучить документацию к вашему 3д-редактору.
- В случае если программа принтера делает замечание по STL файлу после генерации задания – рекомендуем скачать и использовать программы, исправляющие ошибки STL (например: Netfabb Studio Basic ).
- Не размещайте слишком много моделей в один STL файл. Всегда проще работать, когда в файле находится одна деталь.
- Располагайте модель в пространстве так, чтобы при печати было меньше выступов с поддержками. Это упростит печать и улучшит качество готового образца.

Сервис и поддержка

- Раз в месяц производите смазку направляющих принтера по которым движутся подшипники. Используйте обычное машинное масло или специальные смазки для подшипников.

•

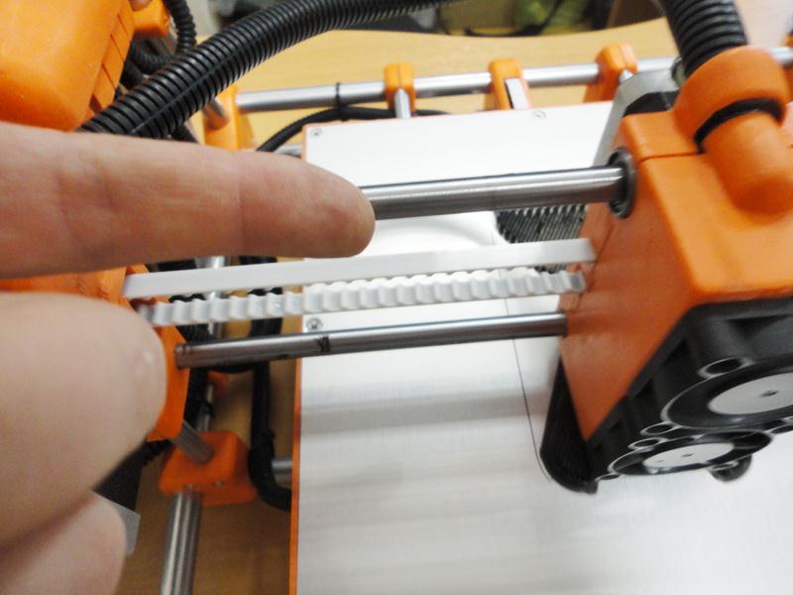
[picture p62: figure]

- Если качество печати сильно ухудшилось – смените сопло. Оно является расходным материалом. Однако служить может очень долго, при правильной эксплуатации и следовании рекомендациям: отмочить сопло можно в активном растворителе или дихлорэтане. Так же очень помогают избавиться от нагара ультразвуковые ванны. Не используйте грязный или пыльный пластик.
- Следите за движущимися частями принтера, чтобы в них не попадали посторонние предметы и грязь.
- Если в результате сильного механического воздействия платформа перекосилась – ее можно поправить и отъюстировать винтами, находящимися под платформой. См. фото:

•

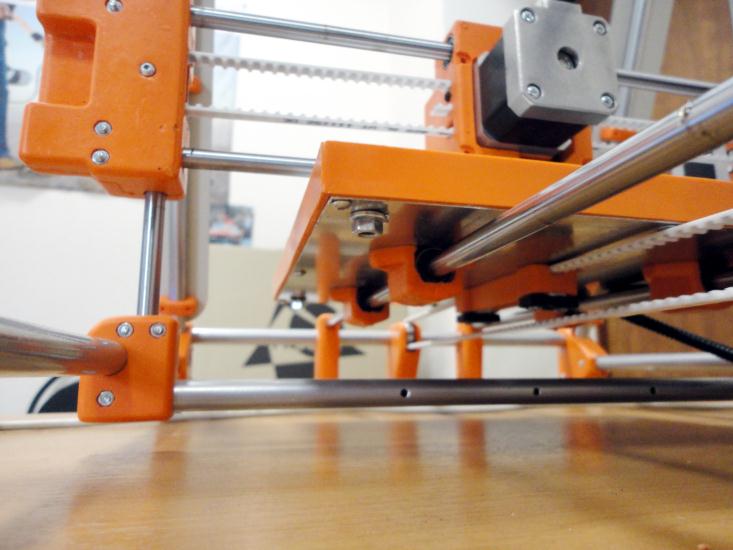
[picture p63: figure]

- В случае если сопло экструдера слишком прижимается к платформе (это видно при печати первого слоя) – остановите печать, зайдите в меню Сервис – Корректировка смещения оси
Z. Там Вы сможете плавно настроить «ноль» по высоте. При этом сопло должно быть выше платформы с наклеенной пленкой на толщину бумажного листа от принтера.
- По всем вопросам Вы можете обратиться к нам за консультацией, по указанным ниже контактам.

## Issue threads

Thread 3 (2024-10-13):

Боковые прижимы энкодеров

ACKET2009, 2024-10-13:
Здравствуйте! У меня на принтере Picaso XL PRO сломан корпус энкодеров. У вас есть STL файл для печати нового корпуса, но нет боковых прижимов которые вдвигаются на ласточкин хвост в корпус. На моём корпусе эти детали целые, но с одной стороны деталь с одним шипом, а с другой с 2мя шипами, а в этой модели корпуса предполагается установка боковинок однотипных с 2мя шипами...

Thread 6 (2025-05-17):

PRO 250 \ Крепление для катушек пластика

BarrtyG, 2025-05-17:
Здравствуйте, не нашел крепление на катушку под пластик для своего Picaso PRO 250.
Скажите пожалуйста файл по ссылке - этот тот оно, новая версия?
[STL_Детали_принтеров/PRO250/PRO250_Кронштейн.stl](https://github.com/Octopusmode/Picaso3D/blob/master/STL_%D0%94%D0%B5%D1%82%D0%B0%D0%BB%D0%B8_%D0%BF%D1%80%D0%B8%D0%BD%D1%82%D0%B5%D1%80%D0%BE%D0%B2/PRO250/PRO250_%D0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)

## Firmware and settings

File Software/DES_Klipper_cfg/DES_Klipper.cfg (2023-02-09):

[mcu]
###############
## USB-mode ##
###############
serial: /dev/serial/by-id/usb-Klipper_lpc1769_12345-if00
restart_method: command

[virtual_sdcard]
path: /home/klipper/printer_data/gcodes

[display_status]
              
[input_shaper]

[pause_resume]
recover_velocity: 80
         
#[firmware_retraction]
#retract_length: 3
#retract_speed: 40
#unretract_speed: 40


#############
## PRINTER ##
#############
[printer]
kinematics: corexy
max_velocity: 130
max_accel: 3000
max_z_velocity: 10
max_z_accel: 30
square_corner_velocity: 5.0

############  
## X-AXIS ##
############
[stepper_x]
enable_pin:   !P2.1
step_pin:      P2.2
dir_pin:      !P2.6
endstop_pin:  P1.29
microsteps: 16
rotation_distance: 37.5
position_endstop: -7
position_min: -7
position_max: 210
homing_speed: 40


############
## Y-AXIS ##
############
[stepper_y]
enable_pin:   !P2.8
step_pin:      P0.19
dir_pin:      !P0.20
endstop_pin:  P1.28
microsteps: 16
rotation_distance: 37.5
position_endstop: 0
position_min: 0
position_max: 203
homing_speed: 40


############
## Z-AXIS ##
############
[stepper_z]
enable_pin:   !P0.21
step_pin:      P0.22
dir_pin:      P2.11
endstop_pin:  ^P1.27
microsteps: 16
rotation_distance: 4
position_min: -1
position_max: 162
#position_endstop: 0



[safe_z_home]
home_xy_position: 104,203
speed: 40
z_hop: 2
z_hop_speed: 5


 
##############
## EXTRUDER ##
##############
[extruder]
enable_pin: !P2.12
step_pin:   P2.13
dir_pin:    P0.11
microsteps: 16
rotation_distance: 1.807
nozzle_diameter: 0.400
filament_diameter: 1.750
heater_pin: P2.7
sensor_type: Generic 3950
#sensor_pin: therm:PK7
#control: pid
#pid_Kp: 22.2
#pid_Ki: 1.08
#pid_Kd: 114
min_temp: 0
max_temp: 290
sensor_pin:  P0.24

[thermistor Trianglelab-NTC100K-B3950]
temperature1: 25
resistance1: 100000.0
temperature2: 150
resistance2: 1791.0
temperature3: 250
resistance3: 283.0
#########
## BED ##
#########
[heater_bed]
heater_pin:	 P2.5
sensor_type: EPCOS 100K B57560G104F
sensor_pin:  P0.25

min_temp: 0
max_temp: 130

control: pid
pid_Kp: 75.139
pid_Ki: 2.636
pid_Kd: 535.368

###########################
## FAN0 Part cooling fan ##
###########################
[fan]
pin: P2.3
kick_start_time:  0.1
off_below:  0.2
#######################################
## FAN1 Extruder fan (connected HE1) ##
#######################################
[heater_fan hfan]
pin: P2.4
heater_temp: 50

############
## X-AXIS ##
############
#[tmc2209 stepper_x]
#uart_pin: 			 P1.10 
#microsteps: 		 32 
#interpolate:     True
#run_current: 		 1.000
#hold_current: 	 0.500
#stealthchop_threshold: 500
############
## Y-AXIS ##
############
#[tmc2209 stepper_y]
#uart_pin: 			  P1.9
#microsteps: 			32
#interpolate:      True
#run_current: 		  1.000
#hold_current: 		0.500
#stealthchop_threshold: 500
############
## Z-AXIS ##
############
#[tmc2209 stepper_z]
#uart_pin: 			  P1.8
#microsteps: 			32
#interpolate:      True
#run_current: 		  1.000
#hold_current: 		0.500
#stealthchop_threshold: 500
##############
## EXTRUDER ##
##############
#[tmc2209 extruder]
#uart_pin: 			  P1.4 
#microsteps: 			16
#run_current: 		  0.800
#hold_current: 		0.500
#stealthchop_threshold: 	 5

########################################
# EXP1 / EXP2 (display) pins
########################################
[board_pins]
aliases:
    # EXP1 header
    EXP1_1=P1.30, EXP1_3=P1.18, EXP1_5=P1.20, EXP1_7=P1.22, EXP1_9=<GND>,
    EXP1_2=P0.28, EXP1_4=P1.19, EXP1_6=P1.21, EXP1_8=P1.23, EXP1_10=<5V>,
    # EXP2 header
    EXP2_1=P0.17, EXP2_3=P3.26, EXP2_5=P3.25, EXP2_7=P1.31, EXP2_9=<GND>,
    EXP2_2=P0.15, EXP2_4=P0.16, EXP2_6=P0.18, EXP2_8=<RST>, EXP2_10=<NC>
    
# Pins EXP2_1, EXP2_6, EXP2_2 are also MISO, MOSI, SCK of bus "ssp0"

[display]
lcd_type: hd44780
rs_pin: EXP1_4
e_pin: EXP1_3
d4_pin: EXP1_5
d5_pin: EXP1_6
d6_pin: EXP1_7
d7_pin: EXP1_8
#   The pins connected to an hd44780 type lcd. These parameters must
#   be provided.
hd44780_protocol_init: true
#   Perform 8-bit/4-bit protocol initialization on an hd44780 display.
#   This is necessary on real hd44780 devices. However, one may need
#   to disable this on some "clone" devices. The default is True.
line_length: 20
#   Set the number of characters per line for an hd44780 type lcd.
#   Possible values are 20 (default) and 16. The number of lines is
#   fixed to 4.
encoder_pins: ^EXP2_5, ^EXP2_3
click_pin: ^!EXP2_7
#####################
## BED CALIBRATION ##
#####################

[bed_mesh]
speed: 120
horizontal_move_z: 5
mesh_min: 35, 6
mesh_max: 184, 170
probe_count: 3, 3


#############
## MACROS  ##
#############

[gcode_macro PAUSE]
description: Pause the actual running print
rename_existing: PAUSE_BASE
# change this if you need more or less extrusion
variable_extrude: 1.0
gcode:
  ##### read E from pause macro #####
  {% set E = printer["gcode_macro PAUSE"].extrude|float %}
  ##### set park positon for x and y #####
  # default is your max posion from your printer.cfg
  {% set x_park = printer.toolhead.axis_maximum.x|float - 5.0 %}
  {% set y_park = printer.toolhead.axis_maximum.y|float - 5.0 %}
  ##### calculate save lift position #####
  {% set max_z = printer.toolhead.axis_maximum.z|float %}
  {% set act_z = printer.toolhead.position.z|float %}
  {% if act_z < (max_z - 2.0) %}
      {% set z_safe = 2.0 %}
  {% else %}
      {% set z_safe = max_z - act_z %}
  {% endif %}
  ##### end of definitions #####
  PAUSE_BASE
  G91
  {% if printer.extruder.can_extrude|lower == 'true' %}
    G1 E-{E} F2100
  {% else %}
    {action_respond_info("Extruder not hot enough")}
  {% endif %}
  {% if "xyz" in printer.toolhead.homed_axes %}
    G1 Z{z_safe} F900
    G90
    G1 X{x_park} Y{y_park} F6000
  {% else %}
    {action_respond_info("Printer not homed")}
  {% endif %} 


[gcode_macro RESUME]
description: Resume the actual running print
rename_existing: RESUME_BASE
gcode:
  ##### read E from pause macro #####
  {% set E = printer["gcode_macro PAUSE"].extrude|float %}
  #### get VELOCITY parameter if specified ####
  {% if 'VELOCITY' in params|upper %}
    {% set get_params = ('VELOCITY=' + params.VELOCITY)  %}
  {%else %}
    {% set get_params = "" %}
  {% endif %}
  ##### end of definitions #####
  {% if printer.extruder.can_extrude|lower == 'true' %}
    G91
    G1 E{E} F2100
  {% else %}
    {action_respond_info("Extruder not hot enough")}
  {% endif %}  
  RESUME_BASE {get_params}

[gcode_macro CANCEL_PRINT]
description: Cancel the actual running print
rename_existing: CANCEL_PRINT_BASE
gcode:
  TURN_OFF_HEATERS
  CANCEL_PRINT_BASE

#*# <---------------------- SAVE_CONFIG ---------------------->
#*# DO NOT EDIT THIS BLOCK OR BELOW. The contents are auto-generated.
#*#
#*# [stepper_z]
#*# position_endstop = -0.605
#*#
#*# [extruder]
#*# control = pid
#*# pid_kp = 34.180
#*# pid_ki = 2.212
#*# pid_kd = 132.022

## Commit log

2022-10-24 Первый коммит!
2022-10-24 Профили перемещены в отдельную папку
2022-11-03 Загрузка
    Папка Сопливчики_форма_для_литья
    [Литейная форма для чистиков х4.step, Литейная_форма_для_чистиков_х4_часть_1_с_допуском.stl, Литейная_форма_для_чистиков_х4_часть_2_с_допуском.stl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]
2022-11-03 Update README.MD
    Ссылка на центр поддержки
2022-11-08 Скачано всё, что было в гугл драйве
    [2 DPX 00.00.05 Держатель катушки.STL, 2 DPX 02.00.16 Держатель чистика V1 NEW.STL, DPS 004.10.08 Филамент.STL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]
2022-11-08 Удаление задвоенного
    Удалила Несортированное/Держатель катушки, так как это уже есть в файлах.
    [Вал внешний.stl, Ось.stl, Подвес.stl]
2022-11-08 Удален дубляж
    Удален дубляж из Несортированное\Picaso тесты
    [Настройка_прижима.STL]
2022-11-08 Удален дубляж_2
    Удален дубляж их Несортированное\Picaso модели
    [Форма_для_отливки.stl]
2022-11-08 Несортированное
    Переместила, разобрала дубляжи из Несортированное\Picaso модели\X Pro
    [DPX_00.00.05+Держатель_катушки.STL, DPX_02.00.16_Держатель_чистика_V1.STL, Фиксатор трубок X Pro v3.stl]
2022-11-08 Переименование файлов
    [Петля.STL, Фиксатор трубок X Pro v3.stl]
2022-11-08 Разобрала Software_Firmware
    Переименование, сортировка по папкам. Вынесла папку Software_Firmware в основную папку Picaso3D
2022-11-13 Несортированное
    [250PRO_Y_Shaft_holder.stl, 250PRO_Y_endstop.stl, 250PRO_Кронштейн.stl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]
2022-11-18 Переименование
    [Настройка_прижима_200x200.stl]
2022-11-21 Other
    Уменьшение размера картинок, редактирование READMEs
    [2_Петля_в_сборе.STL, DPX_00.00.12_Контейнер_левый.STL, DPX_00.00.13_Контейнер_правый.STL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]
2022-11-22 Подшипники Ы1
2022-11-22 Other
    Уменьшено разрешение картинок
2022-11-26 Ножки для корпуса
    [LeftFront_V2.stl, Rear_V2.stl, RightFront_V2b.stl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]
2022-11-26 Cura (under construction)
    Ремонтирую описание Куры. Добавила статью про Симпли, пошуршала над почти всеми картинками
    [LeftFront_V2.stl, Rear_V2.stl, RightFront_V2b.stl]
2022-11-26 Редактирование img
2022-11-26 Update README.md
    Редактирование разметки
2022-11-28 Блоки энкодера DXPRO S1/S2 STL
    [Des X PRO блок энкодеров 1.STL, Блок энкодеров X PRO rev. 1.STL, Копия Des X PRO блок энкодеров 2.STL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]
2022-11-28 Энкодеры
    [XPRO_Блок_энкодеров_S2.STL, XPRO_Блок_энкодеров_rev_1_S1.STL, XPRO_Крышка_блока_энкодеров_S1.STL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]
2022-11-30 Вентилятор_обдува
    [4020_front_fan_DX_mod.STL, 4020_rear_fan_DX_mod.STL]
2022-11-30 Вентилятор_обдува_Х
    [4020_front_fan_DX_mod.STL, 4020_rear_fan_DX_mod.STL]
2022-11-30 Покупные_ЭРИ
2022-12-17 Радиоэлементы
2023-02-24 sources added
    [Литейная_форма_для_чистиков_х4.step]
2023-06-12 Update Содержимое репозитория копия.md
2024-04-22 файлы крепления катущек
    [Держалка_катушек_Пикасо_крепеж.stl, Держалка_катушек_Пикасо_труба_45.stl, Держалка_катушек_Пикасо_труба_65.stl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]
2024-04-26 Корректировка оформления
2024-04-26 Корректировка офомления
2024-11-09 Добавлен полигон версии 2.6.20
2024-11-09 Обновлен .gitignore
2024-11-09 Добавлен ваниант держателья катушек
    [NutSucond.stl, Picaso spool holder v9.3mf, Spool holder picaso nut.stl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]
2024-11-23 Добавлены профили для OrcaSlicer и PrusaSliver
